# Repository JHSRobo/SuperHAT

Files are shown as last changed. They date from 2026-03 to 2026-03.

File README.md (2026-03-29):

# SuperHAT V2

A HAT (hardware attached on top) for the Raspberry Pi 4 & 5. 

---

## Power Rail Breakdown

SuperHAT receives external 5V and 12V power (with a common ground) from an [MR30 connector](https://www.tme.com/us/en-us/details/mr30pw-m/dc-power-connectors/amass/). 12V is used for tools and motors. 5V is used for tools, servos, and powering the Raspberry Pi. When using the SuperHAT, do not plug in a USB-C power supply. 

---

## Feature Overview

1. **Four** N-type MOSFETs for GPIO switching 5V or 12V tools.
2. **Six** connectors for I²C interfacing.
3. **One** dual H-bridge 12V motor driver.
4. **One** stepper motor driver
5. **Two** 5V servo connectors
6. Overvoltage Protection
7. Voltage & Current Sensing

### 1. MOSFET GPIO Switching

#### Schematic



#### N-Type MOSFET

The N-type MOSFET ([AOSS32136C](https://www.digikey.com/en/products/detail/alpha-omega-semiconductor-inc/AOSS32136C/11567433)) in the schematic is routed for low-side switching. When testing, switching on the high side (before the load), resulted in a voltage drop. In an underwater environment, employing low-side switching means that the wires leading to the tool will be high (5V or 12V) when the tool is idling. 

#### Back-EMF Protection

There is a standard diode ([GSD2004WS-HE3-08](https://www.digikey.com/en/products/detail/vishay-general-semiconductor-diodes-division/GSD2004WS-HE3-08/4831745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)) on the 5V and 12V lines. When the load is switched off, the diode prevents sensitive electronic components (the MOSFET in this case) from receiving voltage spikes generated by an inductive load (e.g. motor). 

#### 5V Configuration

To use a 5V you will need to solder the jumper (on the back of the board). Do not use a 12V tool when you solder the jumper because the 12V and 5V lines will short (because JP7 is closed and D3 leads to 5V). Technically, since MOSFETs can behave like variable resistors, and sending a PWM signal can "adjust" the voltage of the gate, it is possible to operate lower voltage tools. However, this is not recommended as there is no RC-filter at the gate to smooth these pulses. This RC-filter will be a feature in SuperHAT V3.

#### LED Indicator & Pulldown Resistor

In the schematic, there is an additional 10k $\Omega$ pulldown resistor in parallel with the LED circuit. This is because the LED can’t instantly pull down the voltage (since LEDs are non-ohmic). Intuitively, the green LED turns on when the GPIO is high. 

### 2. I²C Interfacing

#### Schematic



#### Connectors

To ensure connectivity with a wide range of devices, there are six "I²C connectors": two [right-angle JST-SH](https://www.digikey.com/en/products/detail/jst-sales-america-inc/SM04B-SRSS-TB/926710), two [vertical JST-SH](https://www.digikey.com/en/products/detail/jst-sales-america-inc/BM04B-SRSS-TB/926696), and two [right-angle JST-GH](https://www.digikey.com/en/products/detail/jst-sales-america-inc/SM04B-GHS-TB/807788) connectors. Note that JST-SH is  the same as STEMMA QT by Adafruit and Qwiic by Sparkfun. 

#### Pull-ups

There are no pullups for I²C on SuperHAT because the Raspberry Pi already incorporates 1.8k $\Omega$ pull-up resistors for SCL and SDA lines. 

#### 5V Device Support

Connector J10 is specifically designed for 5V I²C devices. While this connector provides 5V power to the device, the SDA and SCL logic lines remain at 3.3V levels. Ensure connected devices are 3.3V logic-compatible or include appropriate level-shifting circuitry.

### 3. Dual H-Bridge Motor Driver

#### Schematic



#### Operation

A 12V brushed DC motor can be driven in both directions with the [DRV8871](https://www.digikey.com/en/products/detail/texas-instruments/DRV8871DDARQ1/7244177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) motor driver. Input pins are set to GPIOs 9 and 10. To drive the motor, set one of the pins to high, and the other to low. Flip the status of both pins to drive the motor in the opposite direction. The motor won't move went both GPIOs are set to low. The 30k $\Omega$ resistor on pin 4 (ILIM) results in a trip current of about 2A (64 (kV) / R<sub>ILIM</sub> (k $\Omega$)). 

### 4. Stepper Motor Driver

#### Schematic



#### Operation

A 12V stepper motor can be driven by this motor driver ([DRV8825](https://www.digikey.com/en/products/detail/texas-instruments/DRV8825PWPR/2695909)). The pins for operation are GPIOs 21 and 26. Pulse GPIO 21 to move the stepper motor and set GPIO 26 to low or high to determine the direction of rotation. To test the stepper motor, run this code: https://github.com/Harry-IV/superhat_test/blob/main/stepper_motor.py.

#### Settings

To adjust the current limiting, use the screwhead on the potentiometer. The current limit is the voltage read on the screw head of the potentiometer multiplied by 2. To disable the stepper motor driver, solder jumper JP6. 

#### Cooling

This IC gets hot, especially at higher currents. It would be wise to put a heat-sink.

### 5. Servo Driving

#### Schematic



#### Operation

GPIOs 12 and 13 can each drive one servo motor (a total of two for SuperHAT). Having a direct connection, especially with a Raspberry Pi due to their timing inconsistencies, can lead to jitter. This can be mitigated by using the [pigpio library](https://abyz.me.uk/rpi/pigpio/) or by "sleeping" the pin while not moving the servo. 

### 6. Overvoltage Protection

#### Schematic



#### Undervoltage Lockout (UVLO)

The [TPS259621](https://www.digikey.com/en/products/detail/texas-instruments/TPS259621DDAR/10445382) will cut off power to the Raspberry Pi completely if the EN/UVLO pin does not receive a voltage above 1.2V (when rising). The UVLO threshold is set by a voltage divider consisting of resistors R18 (7.5kΩ) and R19 (2.61kΩ). These values yield an undervoltage cutoff of 4.85V. Note that the undervoltage cutoff when falling will be lower since it will cut off when the EN/UVLO pin does not receive a voltage above 1.1V. Ultimately, this part of the circuit isn’t really that necessary.

#### Overvoltage Clamping

What is more necessary is the overvoltage component. Here, there is no voltage divider. Texas Instrument's documentation calls for a 400k ohm resistor for the output clamp voltage to be 5.45V, but a 470k ohm resistor is used instead because they are a lot easier to come by. 

#### Additional Resources

Video explanation by GreatScott!: https://www.youtube.com/watch?v=JOhQ3nsR7xo&t=440s 

### 7. Voltage and Current Sensing

#### Schematic



#### INA3221

The [INA3221](https://www.digikey.com/en/products/detail/texas-instruments/INA3221AQRGVRQ1/5995432) is a digital power-sensing IC that communicates via I²C. It features 3 channels, which are used to measure the voltage and current on the 3.3V, 5V, and 12V rails. 

#### Shunt Resistors

Two 0.04 Ω resistors are placed at the 5V and 12V lines near the MR30 connector. All 5V and 12V power on the SuperHAT flows through these two shunts. This includes power draw at 5V from the Pi. A third 0.04 Ω resistor is placed on the 3.3V line near the 3.3V pin from the Raspberry Pi. This does not measure how much current the Pi draws at 3.3V, but rather how much SuperHAT draws (with I²C devices mainly).

#### Testing

To test the INA3221, run this code, which uses Adafruit's INA3221 library: [https://github.com/Harry-IV/superhat_test/tree/main/INA3221]

---

## PCB Layout

### 4-layer Stackup

| Layer | Type |
| ----- | --- |
| 1 | Signal |
| 2 | Ground |
| 3 | Power (3.3V, 5V, 12V) |
| 4 | Signal |



### Design Notes

* Via-in-pad is used to condense routing.
* Copper pours help with thermal dissipation.

---

Email me at harry.c.ohagin@gmail.com if you have any questions.

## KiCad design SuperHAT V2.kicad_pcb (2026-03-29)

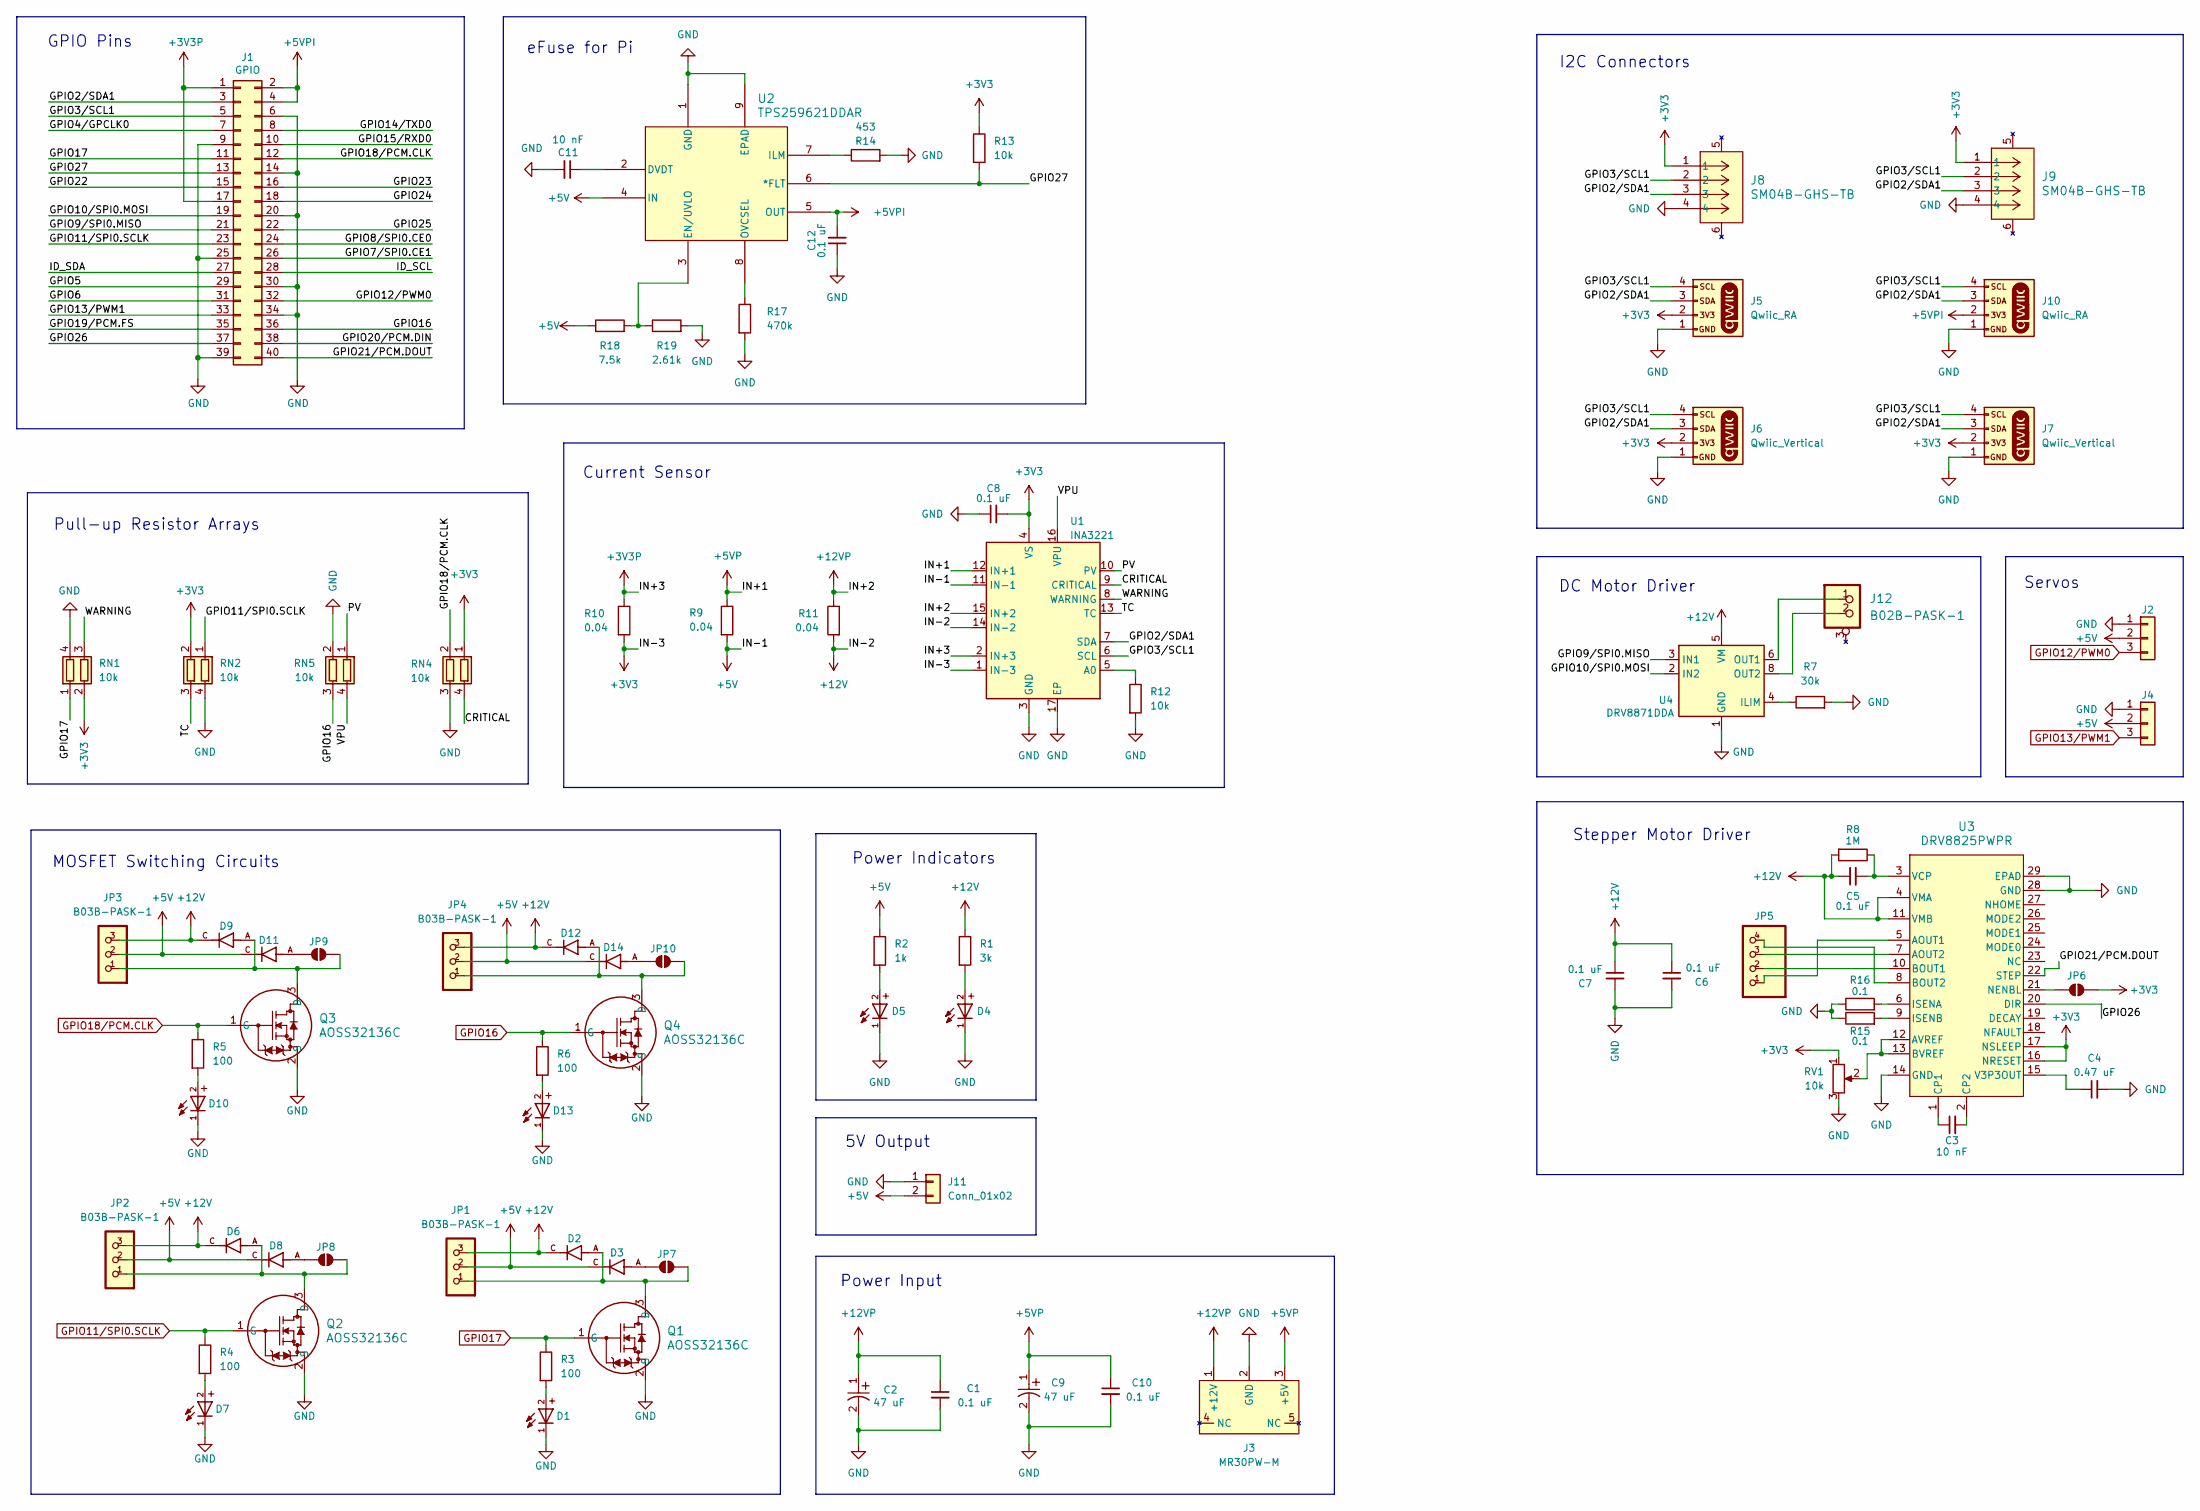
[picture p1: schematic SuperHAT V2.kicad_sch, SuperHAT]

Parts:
C1, C5, C6, C7, C8, C10, C12: 0.1 uF; CAPC2012X140N; Part # C0805C104J5RACAUTO
C2, C9: 47 uF; CAPMP7.6X4.3_3.1N_KEM; Part # T598D476M025ATE060
C3, C11: 10 nF; CAPC2012X140N; Part # C0805C103K5TACAUTO
C4: 0.47 uF; CAPC2012X140N; Part # C0805C474J9RACTU
D1, D7, D10, D13: WL-SMCW_0805; Part # 150080GS75000
D2, D3, D6, D8, D9, D11, D12, D14: SOD2613X115N; Part # GSD2004WS-HE3-08
D4, D5: WL-SMCW_0805; Part # 150080RS75000
J1: GPIO; PinSocket_2x20_P2.54mm_Vertical; Part # PRT-14017
J2, J4: Conn_01x03; PinHeader_1x03_P2.54mm_Vertical; Part # 61300311121
J3: MR30PW-M; AMASS_MR30PW-M_1x03_P3.50mm_Horizontal; Part # MR30PW-M
J5, J10: Qwiic_RA; QWIIC Connector RA; Part # SM04B-SRSS-TB
J6, J7: Qwiic_Vertical; JST_SMD_1.0mm-4_Vertical; Part # BM04B-SRSS-TB
J8, J9: SM04B-GHS-TB; CONN_SM04B-GHS-TB_JST; Part # SM04B-GHS-TB
J11: Conn_01x02; PinHeader_1x02_P2.54mm_Horizontal; Part # 10129379-902002BLF
J12: B02B-PASK-1; CONN_B02B-PASK-1_JST; Part # B02B-PASK-1
JP1, JP2, JP3, JP4: B03B-PASK-1; Part # B03B-PASK-1
JP5: B04B-PASK-1; Part # B04B-PASK-1
JP6, JP7, JP8, JP9, JP10: SolderJumper_2_Open; SolderJumper-2_P1.3mm_Open_TrianglePad1.0x1.5mm
Q1, Q2, Q3, Q4: AOSS32136C; SOT23_AOS; Part # AOSS32136C
R1: 3k; RES_TNPW0805_VIS; Part # TNPW08053K00BEEA
R2: 1k; RES_TNPW0805_VIS; Part # TNPW08051K00BEEA
R3, R4, R5, R6: 100; RES_CHP0805_BRN; Part # CHP0805AFX-1000ELF
R7: 30k; RESC2012X60N; Part # SG73S2ATTD3002F
R8: 1M; RES_CMP0805_BRN; Part # CMP0805AFX-1004ELF
R9, R10, R11: 0.04; RES_VISHAY_WSLP0805_VIS; Part # WSLP0805R0400DEA
R12, R13: 10k; RES_CHP0805_BRN; Part # CHP0805AFX-1002ELF
R14: 453; RESC2012X60N; Part # RN73R2ATTD4530B25
R15, R16: 0.1; RES_VISHAY_WSLP0805_VIS; Part # WSLP0805R1000FEA
R17: 470k; RES_CMP0805_BRN; Part # CMP0805AFX-4703ELF
R18: 7.5k; RES_TNPW0805_VIS; Part # TNPW08057K50BEEA
R19: 2.61k; RES_TNPW0805_VIS; Part # TNPW08052K61BEEN
RN1, RN2, RN4, RN5: 10k; SMT_1002P1AT_VIS; Part # ACASN1002S1002P1AT
RV1: 10k; POT_TC33_3X3P8_BRN; Part # TC33X-1-103ETC33X-1-103E
U1: INA3221; Texas_RGV0016A_VQFN-16-1EP_4x4mm_P0.65mm_EP2.1x2.1mm; Part # INA3221AQRGVRQ1
U2: TPS259621DDAR; SOIC_20DDAR_TEX; Part # TPS259621DDAR
U3: DRV8825PWPR; PWP28_5P18X3P1; Part # DRV8825PWPR
U4: DRV8871DDA; Texas_HTSOP-8-1EP_3.9x4.9mm_P1.27mm_EP2.95x4.9mm_Mask2.4x3.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; Part # DRV8871DDARQ1

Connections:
+3V3: C8.2, J5.2, J6.2, J7.2, J8.1, J9.1, JP6.2 (B), R10.2, R13.1, RN1.2 (R2.1), RN2.2 (R2.1), RN4.1 (R1.1), RV1.1, U1.1 (IN-3), U1.4 (VS), U3.16 (NRESET), U3.17 (NSLEEP)
+3V3P: J1.1, J1.17, R10.1, U1.2 (IN+3)
+5V: D3.C, D8.C, D11.C, D14.C, J2.2, J4.2, J11.2, JP1.2, JP2.2, JP3.2, JP4.2, R2.1, R9.2, R18.1, U1.11 (IN-1), U2.4 (IN)
+5VP: C9.1, C10.1, J3.3 (+5V), R9.1, U1.12 (IN+1)
+5VPI: C12.2, J1.2, J1.4, J10.2, U2.5 (OUT)
+12V: C5.1, C6.1, C7.1, D2.C, D6.C, D9.C, D12.C, JP1.3, JP2.3, JP3.3, JP4.3, R1.1, R8.2, R11.2, U1.14 (IN-2), U3.4 (VMA), U3.11 (VMB), U4.5 (VM)
+12VP: C1.1, C2.1, J3.1 (+12V), R11.1, U1.15 (IN+2)
/CRITICAL: RN4.4 (R1.2), U1.9 (CRITICAL)
/GPIO2/SDA1: J1.3, J5.3, J6.3, J7.3, J8.3, J9.3, J10.3, U1.7 (SDA)
/GPIO3/SCL1: J1.5, J5.4, J6.4, J7.4, J8.2, J9.2, J10.4, U1.6 (SCL)
/GPIO4/GPCLK0: J1.7
/GPIO5: J1.29
/GPIO6: J1.31
/GPIO7/SPI0.CE1: J1.26
/GPIO8/SPI0.CE0: J1.24
/GPIO9/SPI0.MISO: J1.21, U4.3 (IN1)
/GPIO10/SPI0.MOSI: J1.19, U4.2 (IN2)
/GPIO14/TXD0: J1.8
/GPIO15/RXD0: J1.10
/GPIO19/PCM.FS: J1.35
/GPIO20/PCM.DIN: J1.38
/GPIO21/PCM.DOUT: J1.40, U3.22 (STEP)
/GPIO22: J1.15
/GPIO23: J1.16
/GPIO24: J1.18
/GPIO25: J1.22
/GPIO26: J1.37, U3.20 (DIR)
/GPIO27: J1.13, R13.2, U2.6 (*FLT)
/ID_SCL: J1.28
/ID_SDA: J1.27
/PV: RN5.1 (R1.1), U1.10 (PV)
/TC: RN2.3 (R2.2), U1.13 (TC)
/VPU: RN5.4 (R1.2), U1.16 (VPU)
/WARNING: RN1.3 (R2.2), U1.8 (WARNING)
GND: C1.2, C2.2, C4.2, C6.2, C7.2, C8.1, C9.2, C10.2, C11.2, C12.1, D1.1, D4.1, D5.1, D7.1, D10.1, D13.1, J1.6, J1.9, J1.14, J1.20, J1.25, J1.30, J1.34, J1.39, J2.1, J3.2 (GND), J4.1, J5.1, J6.1, J7.1, J8.4, J9.4, J10.1, J11.1, Q1.2 (S), Q2.2 (S), Q3.2 (S), Q4.2 (S), R7.2, R12.2, R14.2, R15.1, R16.1, R17.2, R19.2, RN1.4 (R1.2), RN2.4 (R1.2), RN4.3 (R2.2), RN5.2 (R2.1), RV1.3, U1.3 (GND), U1.17 (EP), U2.1 (GND), U2.9 (EPAD), U3.14 (GND), U3.28 (GND), U3.29 (EPAD), U4.1 (GND), U4.7 (GND), U4.9 (GND)
GPIO11/SPI0.SCLK: J1.23, Q2.1 (G), R4.1, RN2.1 (R1.1)
GPIO12/PWM0: J1.32, J2.3
GPIO13/PWM1: J1.33, J4.3
GPIO16: J1.36, Q4.1 (G), R6.1, RN5.3 (R2.2)
GPIO17: J1.11, Q1.1 (G), R3.1, RN1.1 (R1.1)
GPIO18/PCM.CLK: J1.12, Q3.1 (G), R5.1, RN4.2 (R2.1)
unnamed: D1.2, R3.2
unnamed: D4.2, R1.2
unnamed: D5.2, R2.2
unnamed: D7.2, R4.2
unnamed: D10.2, R5.2
unnamed: D13.2, R6.2
unnamed: JP6.1 (A), U3.21 (NENBL)
unnamed: D2.A, JP1.1, JP7.1 (A), Q1.3 (D)
unnamed: D3.A, JP7.2 (B)
unnamed: D6.A, JP2.1, JP8.1 (A), Q2.3 (D)
unnamed: D8.A, JP8.2 (B)
unnamed: D9.A, JP3.1, JP9.1 (A), Q3.3 (D)
unnamed: D11.A, JP9.2 (B)
unnamed: D12.A, JP4.1, JP10.1 (A), Q4.3 (D)
unnamed: D14.A, JP10.2 (B)
unnamed: R12.1, U1.5 (A0)
unnamed: C11.1, U2.2 (DVDT)
unnamed: R18.2, R19.1, U2.3 (EN/UVLO)
unnamed: R14.1, U2.7 (ILM)
unnamed: R17.1, U2.8 (OVCSEL)
unnamed: JP5.1, U3.5 (AOUT1)
unnamed: JP5.3, U3.7 (AOUT2)
unnamed: RV1.2, U3.12 (AVREF), U3.13 (BVREF)
unnamed: JP5.2, U3.10 (BOUT1)
unnamed: JP5.4, U3.8 (BOUT2)
unnamed: C3.1, U3.1 (CP1)
unnamed: C3.2, U3.2 (CP2)
unnamed: R16.2, U3.6 (ISENA)
unnamed: R15.2, U3.9 (ISENB)
unnamed: C4.1, U3.15 (V3P3OUT)
unnamed: C5.2, R8.1, U3.3 (VCP)
unnamed: R7.1, U4.4 (ILIM)

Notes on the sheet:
5V Output
DC Motor Driver
Stepper Motor Driver
GPIO Pins
Servos
eFuse for Pi
Power Indicators
I2C Connectors
MOSFET Switching Circuits
Pull-up Resistor Arrays
Power Input
Current Sensor

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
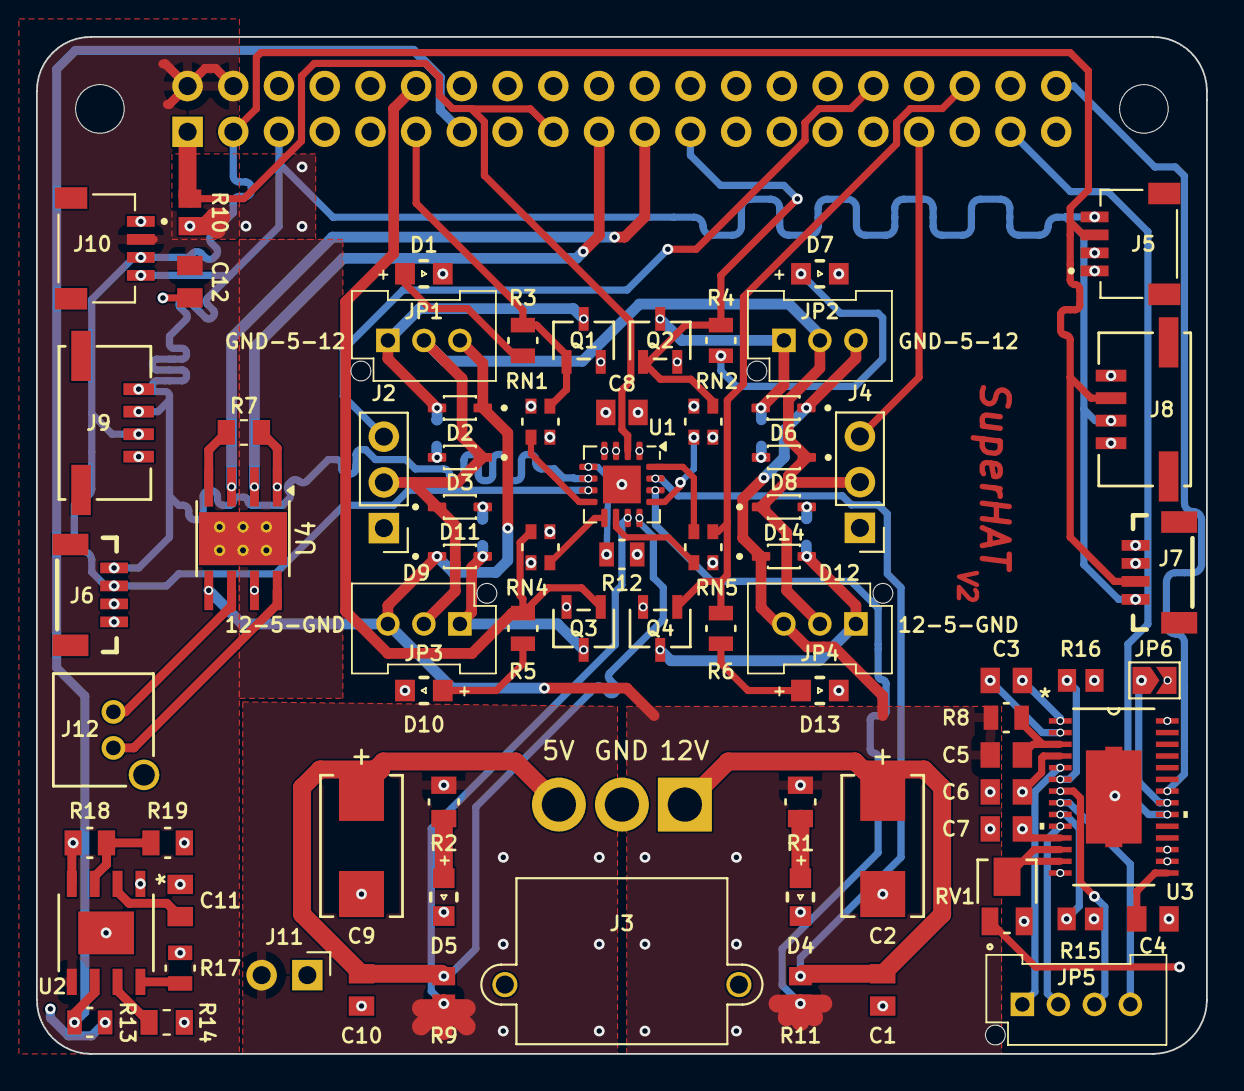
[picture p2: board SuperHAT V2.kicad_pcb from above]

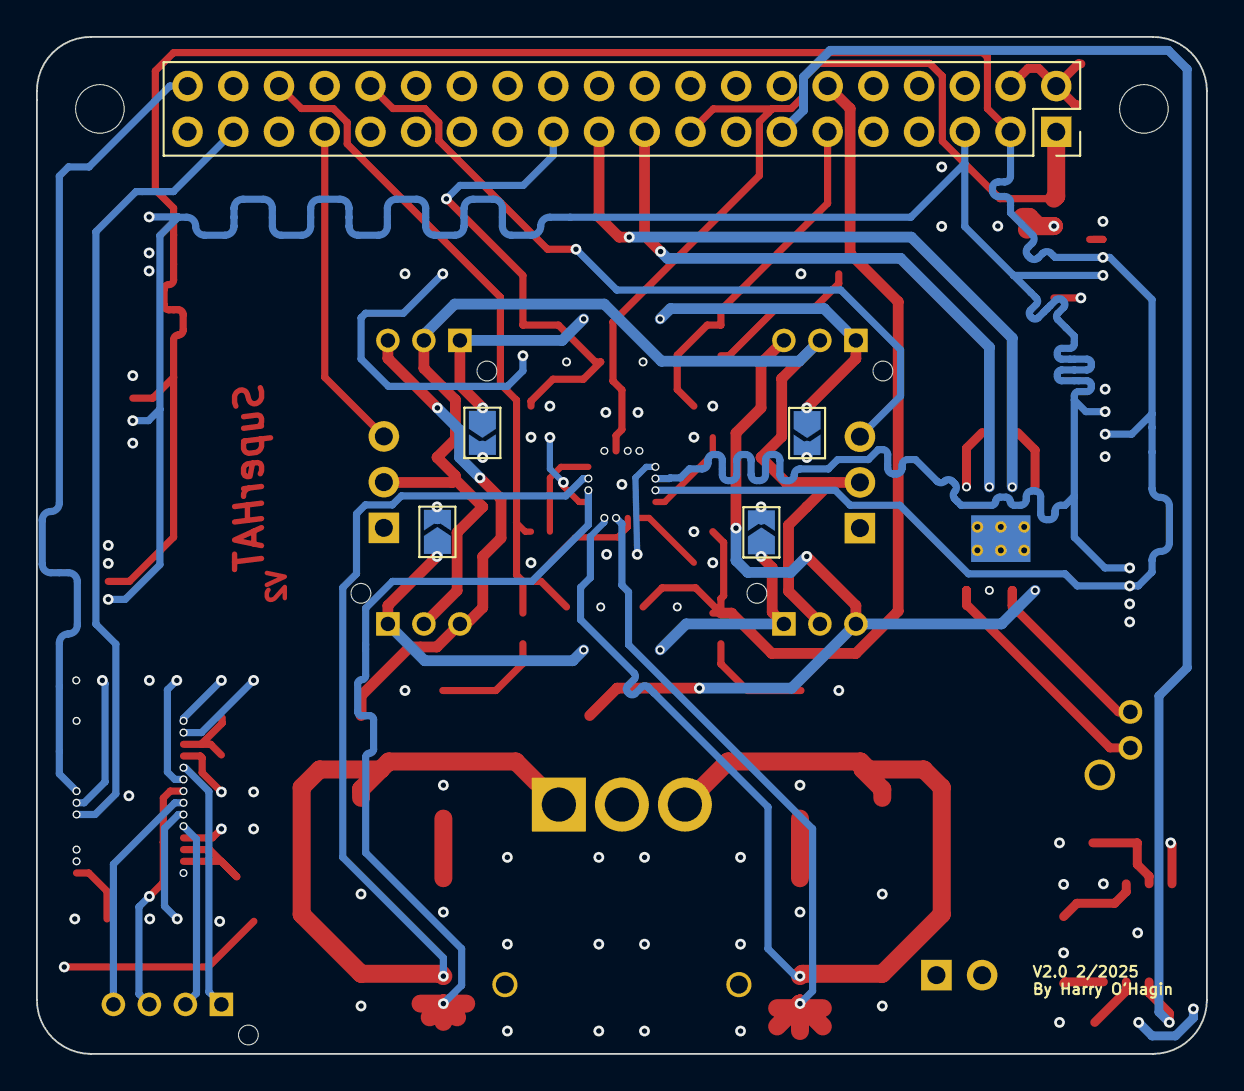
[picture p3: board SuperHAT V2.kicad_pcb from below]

Board: 4 copper layers, 65.0 x 56.5 mm, 82 parts (5 on the bottom side), 60 nets.

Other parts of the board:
MH1, MH2: MountingHole_2.7mm_M2.5
